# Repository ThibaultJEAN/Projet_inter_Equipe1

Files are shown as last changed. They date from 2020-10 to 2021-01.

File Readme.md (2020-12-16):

# I5AEPR11 - Projet interdisciplinaire

> Pauline Combes <br> 
> Emma Devaud <br>
> Romain Gary <br>
> Mélissa Malischewski <br>
> Xavier Bourlot <br>
> Jeremy Aubert <br>
> Clarisse Calmo <br>
> Thibault Jean  <br>
> Xiaohu Zhang <br>

#### [Drive](https://drive.google.com/drive/folders/1-SFvpA1gzc2IVzgCnODUU9VLPYTG9q0a?usp=sharing)

#### [Discord](https://discord.gg/qqvn4z)

#### [Confluence](https://espe.atlassian.net/wiki/spaces/PI/overview?homepageId=131077)

#### [Overleaf Report](https://www.overleaf.com/8144512892ybrzztqnfcqb)

### INSA Toulouse 5A 2020

---

## Buck

`schematic_initial` : Premier schéma pour identifier et calculer les composants critiques

`calculations` : Calcul des composants et contraintes, estimation des pertes

`schematic_complete` : Schéma complet avec composants de mods et indications de routage

---

## BMS

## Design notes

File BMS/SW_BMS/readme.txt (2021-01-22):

************************************************************
*							   *
*		README FILE BMS SOFTWARE		   *
*							   *
************************************************************
author: jeremy aubert for GEI Corp

Utilisation de notre API.

I- Initialisation

Nous proposons une fonction "BMSManagement_Init" permettant
l'initialisation des jauges. Cette initialisation regroupe :
	- la vérification de la bonne connexion entre le 
	microcontroleur et la jauge (avec un mode bloquant
	+ message d'erreur si pas de connexion)

	- l'écriture dans le registre de "control" du mode
	automatique. Cette écriture permet de faire une 
	mise à jour des registres (tension, courant, ...).

Une fonctionnalité n'est tout de fois pas inclu dans cette 
fonction : l'initialisation de la valeur du SOC. D'après
la documentation technique du composant LTC2944, la valeur
par défaut du SOC est de 50%. Pour le moment, il faut 
utiliser la fonction setSOC présente dans InfoBatt.c
Les paramètres à utiliser sont :
	- I2C_HandleTypeDef nb_batt : il faut utiliser
	les constantes BATTERY1 et BATTERY2.
	- uint16_t initValue : il faut entrer la valeur
	en hexadecimal selon le taux de charge de la 
	batterie. Cette valeur se fixe selon la formule
	suivante :
	     (initValue)_16=deltaQ*StateOfCharge

II- La lecture des informations se fait par la fonction 
BMSManagement_getInfo. Les paramètres sont :
	- char info : 'V' pour avoir la tension, 'I' pour
	avoir le courant, 'S' pour avoir le SOC.
	- I2C_HandleTypeDef nb_batt : il faut utiliser
	les constantes BATTERY1 et BATTERY2.

III- Fonction support

saveSOC - Afin de sauvegarder la dernière valeur de SOC
des batteries pour la sauvegarder dans une mémoire.

checkLink - A utiliser si vous souhaitez vérifier le lien
à tout moment entre le µC et la jauge.

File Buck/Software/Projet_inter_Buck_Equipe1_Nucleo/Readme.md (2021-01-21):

Indications de fonctionnement pour le code Buck :

PWM sur TIM1. Fréquence réglable par define. Duty min et max aussi. Valeurs actuelles : 150kHz, 10%, 90%
Acquisitions multiples par ADC1 avec DMA et trigger par TIM2, transfert dans les variables par interruption ADC de conversion complète. F_acq réglable par define, valeur actuelle : 5kHz

Les regulations actuelles sont des proportionnel uniquement. Régulation MPPT non fonctionnelle.

Interface Uart (debug rapide) : 
La carte affiche ses mesures toutes les 500ms.
Elle démarre en mode CV 24V.
Pour changer de mode : 'v' pour CV, 'c' pour CC, 'm' pour MPPT, 'o' pour OpenLoop
Pour changer le setpoint : '+' ou '-'. Incrément varie en fonction des modes : CV +-1V, CC +-250mA, OL +-10%.
Attention, ne pas envoyer plusieurs commandes trop rapidement, sinon le buffer panique et il faut reset la carte.

Attention, si la GUI CubeMX est utilisée pour regénérer le projet, il faut ensuite commenter les lignes 
"htim1.Init.Period = 65535;" et "//htim2.Init.Period = 999;".

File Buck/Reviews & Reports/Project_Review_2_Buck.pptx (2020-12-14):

## Smart Power Management System Review n° 2 12-11-2020 INSA Toulouse Team 1 - Buck Xavier Bourlot Thibault Jean Clarisse Calmo Xiaohu Zhang

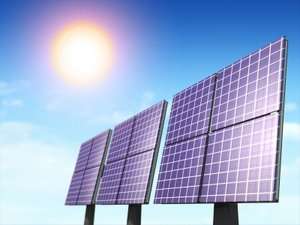
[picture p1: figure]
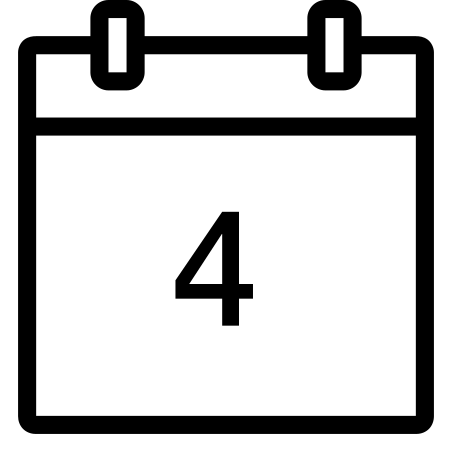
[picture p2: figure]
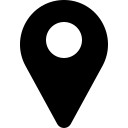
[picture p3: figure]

## TEAM PRESENTATION TEAM SKILLS :

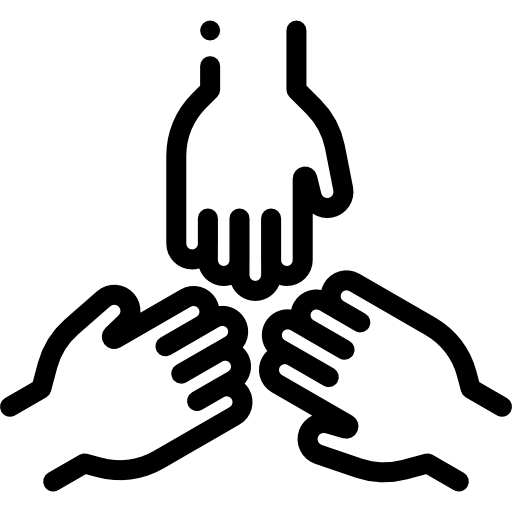
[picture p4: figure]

Team members | Roles
BOURLOT Xavier | Inspector of finished products
CALMO Clarisse | Electronics Engineer / Super Manager
JEAN Thibault | Software and Hardware Engineer
ZHANG Xiaohu | Analog Electronic Engineer

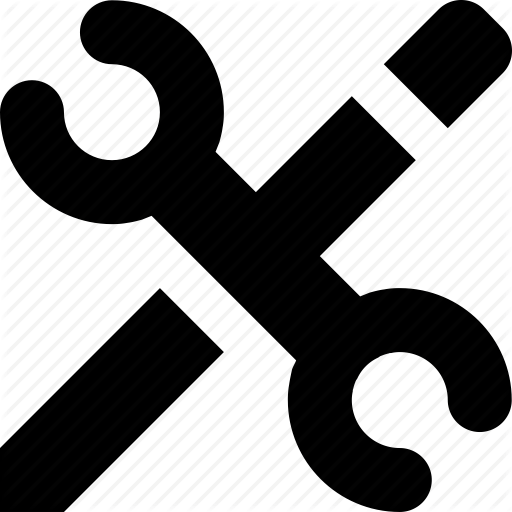
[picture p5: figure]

- Electronic system conception
- Software programming
- Prototyping
- Routing
- Project management
- Cooking

## SYSTEM OVERVIEW

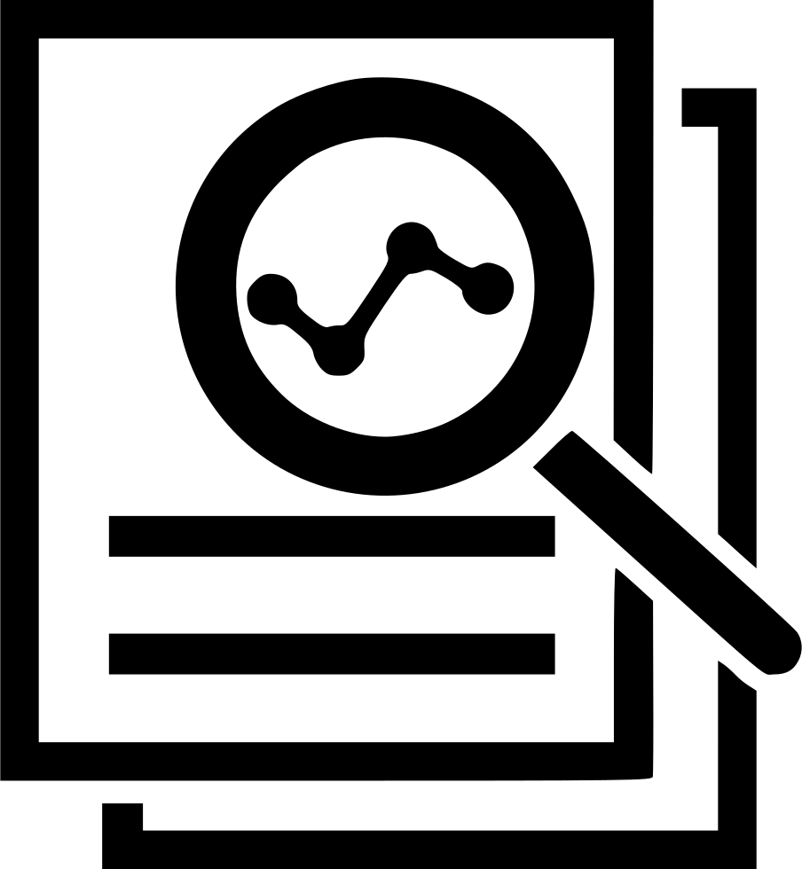
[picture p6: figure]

Smart Power Management System :
intelligent system capable of providing energy, either from power network or from solar panel.

Communicating Plugs :
charges connecting points

Solar Panel Supply Unit : autonomous power block

Buck part :
Energy converter

Our mission : implementing this sub-system.

## HARDWARE ARCHITECTURE

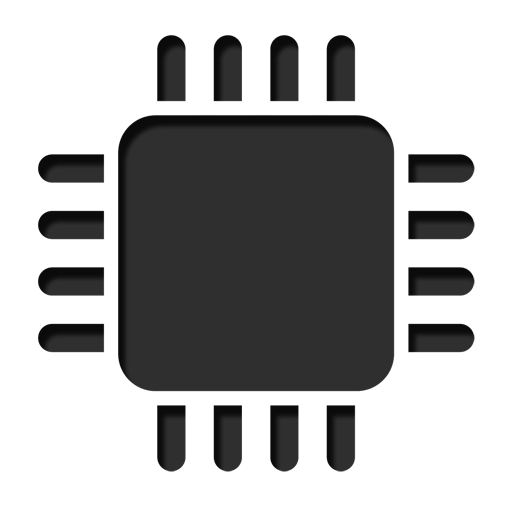
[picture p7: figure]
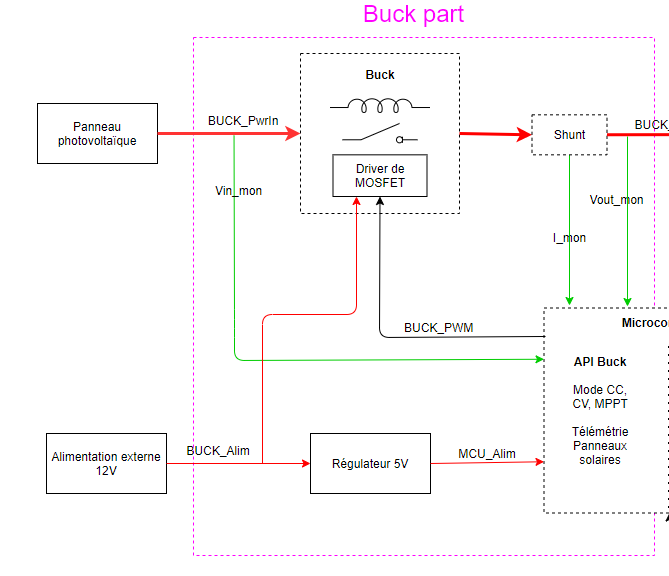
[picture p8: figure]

-Power block located right after the solar panel.
-Energy delivery : up to 200W
-Various control modes :
constant voltage,
constant current,
MPPT,
open loop (test mode)

Towards BMS

Microcontroller

## SOFTWARE ARCHITECTURE

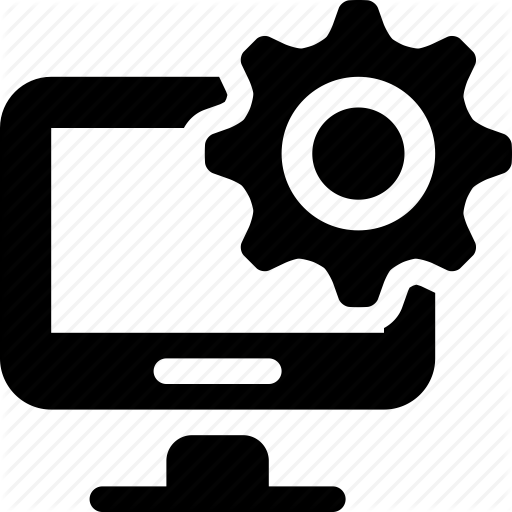
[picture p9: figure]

Software high level architecture
- Function Management_Mode : Management of the different operating modes
- Function Get_BuckOutputCurrent
- Function Get_BuckOutputVoltage
- Function Get_BuckOutputPower
- Function Get_BuckInputVoltage
These different functions are there to retrieve the quantities useful for the regulation modes.

Main specifications we are going to implement :
- The power supply will be taken first from the photovoltaic panel
- Management of the different regulation modes
- Prevention against the risks of too much power and too much discharge of the batteries

## Next steps

The future step of the project are :
- Software development on the project library as well as on the test functions
- Finish composant sizing & selection
- Continue the schematic developpement and start the PCB layout under Altium
- Making further simulations under LTSpice
- Writing a report for the final low level architecture

## Forecast schedule

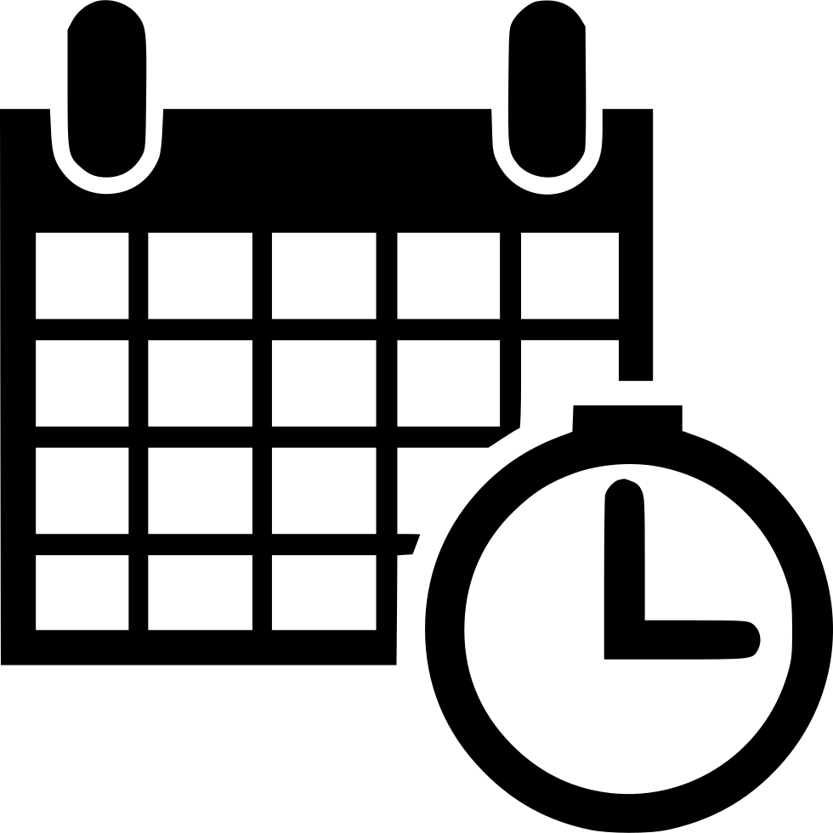
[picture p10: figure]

- This week : finalize the low level architecture
- In 2 weeks : send the final schematic & BOM
- Next month : write a report with the final software architecture
- In 2 months : boards fabrication & write a report with the unit tests

## PREVIOUS REVIEW CONTENT

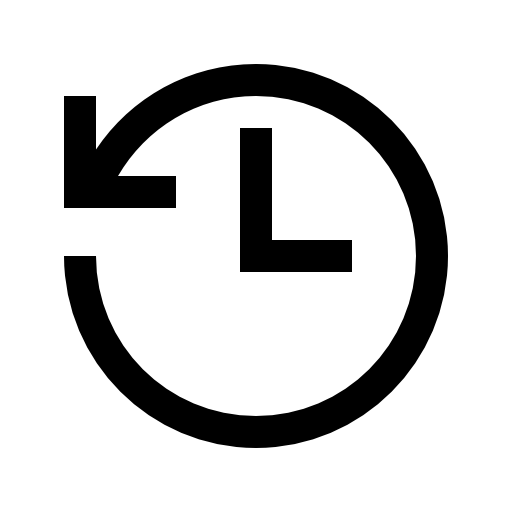
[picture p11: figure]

Last month, we introduced a summary of the work initiated :
- An overview of the smart power management system
- The team skills
- The hardware & software high level architecture
- Our planning

## HARDWARE ADVANCEMENT

Tasks performed since our last meeting :
- Finalize the low level architecture
  - Component selection & sizing
  - Schematic development
  - LTSpice simulations
- Edit project library in Altium
- Edit the BOM
- Finalize the PCB routing

## FINAL HARDWARE SCHEMATIC

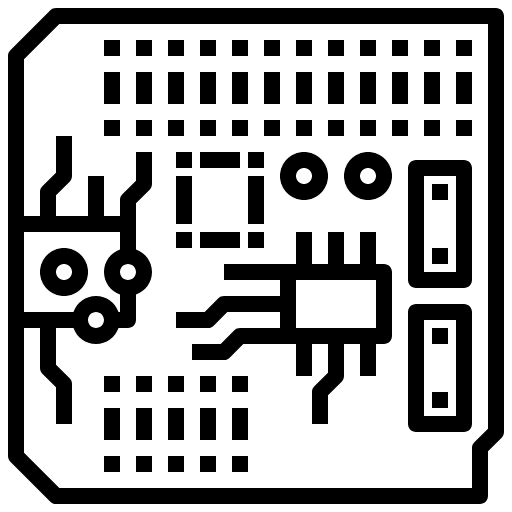
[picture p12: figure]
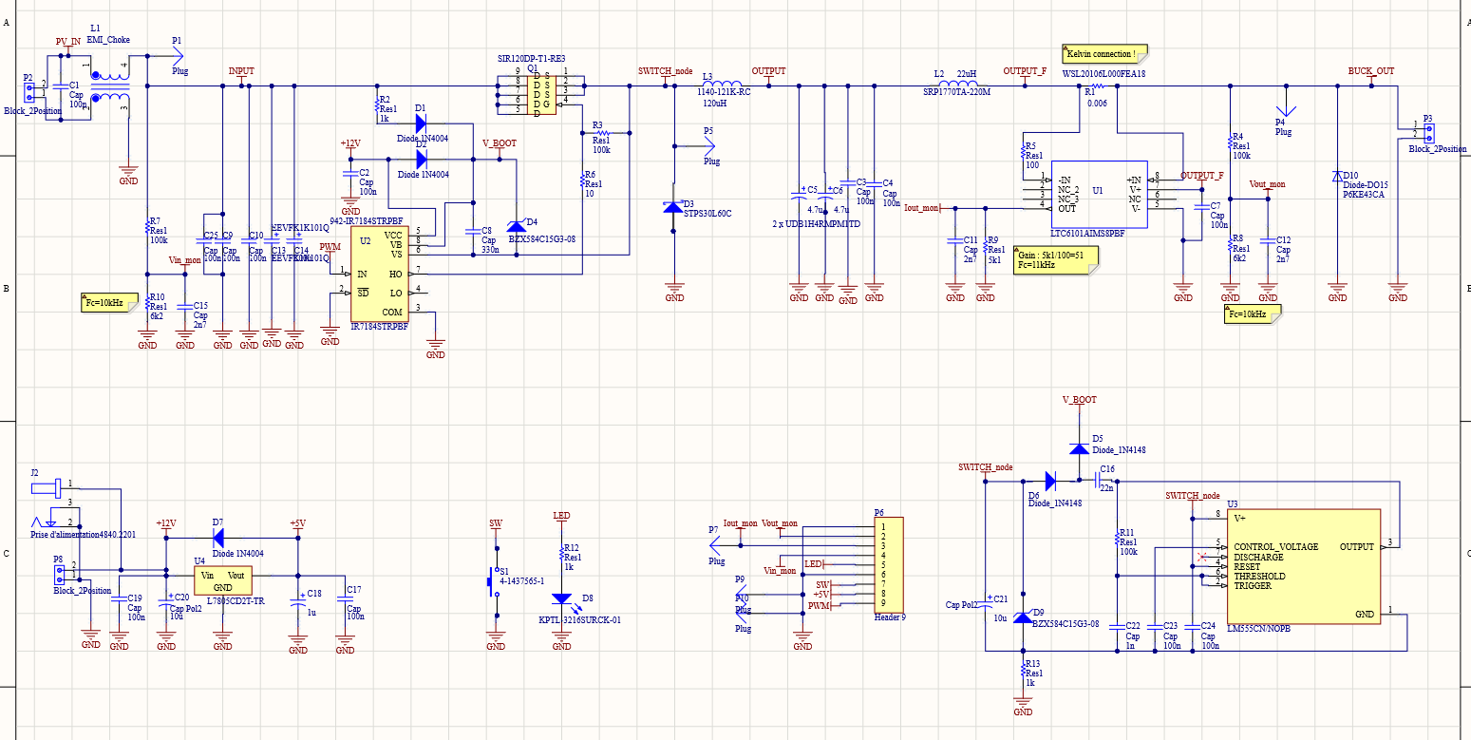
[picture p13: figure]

## ESTIMATED COSTS

- Major costs come from power components
→ power conversion
- EMI (filtering) generates important costs too
→ common mode choke
Costs reduction envisaged :
- Eliminate the external charge pump by restricting the duty cycle in software.
Unsupported costs :
The Nucleo card is shared between the BMS & Buck team.

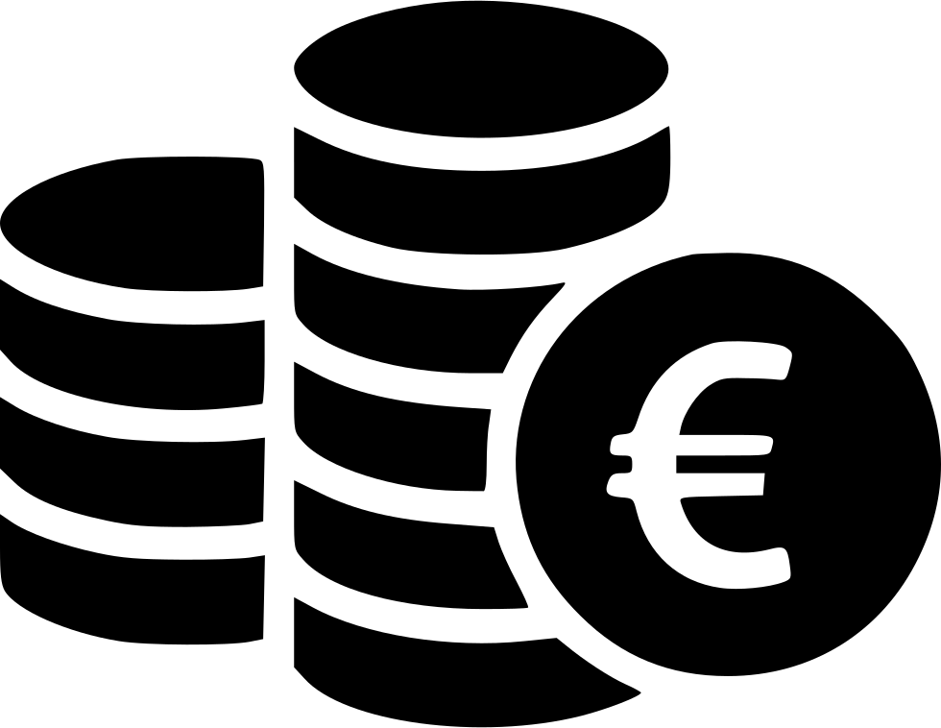
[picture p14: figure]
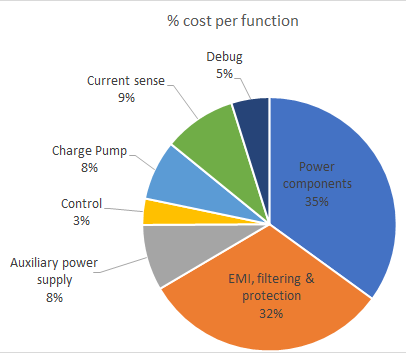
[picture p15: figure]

## PCB ROUTING -2D

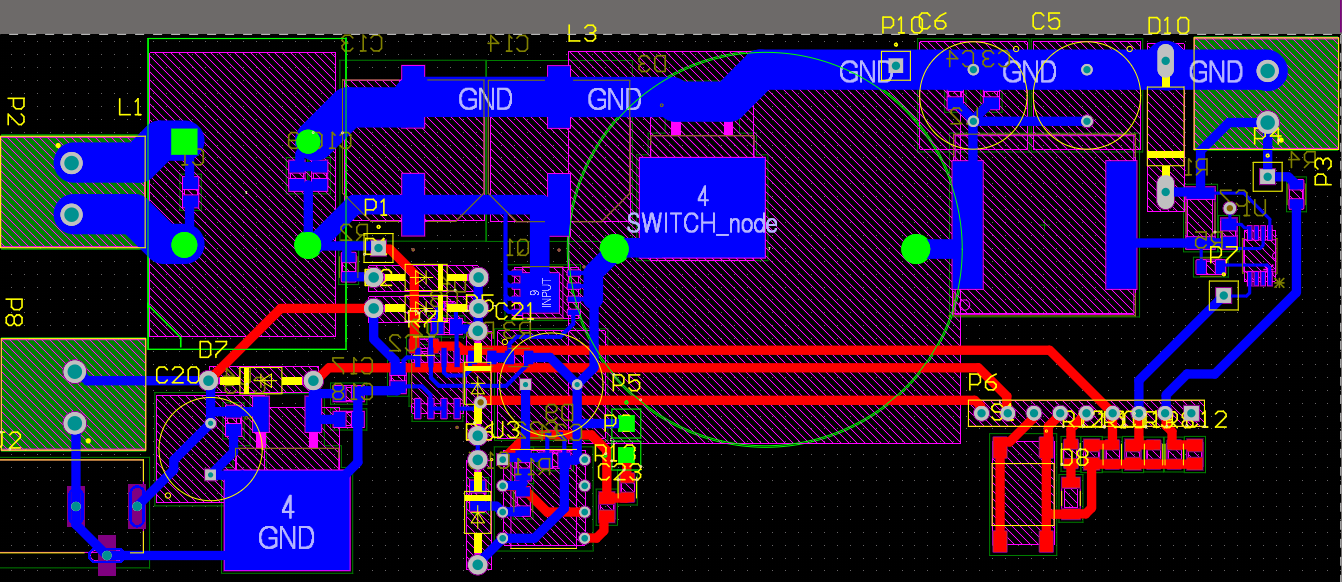
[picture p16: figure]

## PCB ROUTING -3D

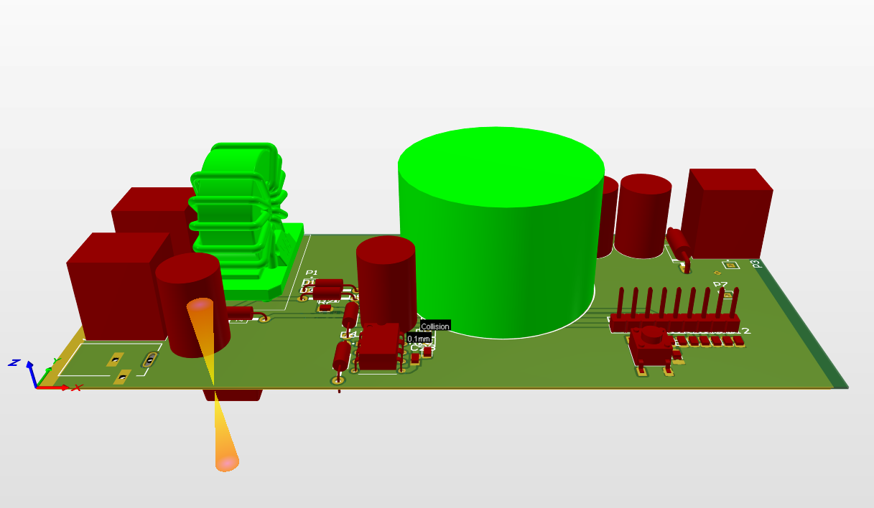
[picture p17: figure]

View of the last version of our PCB design

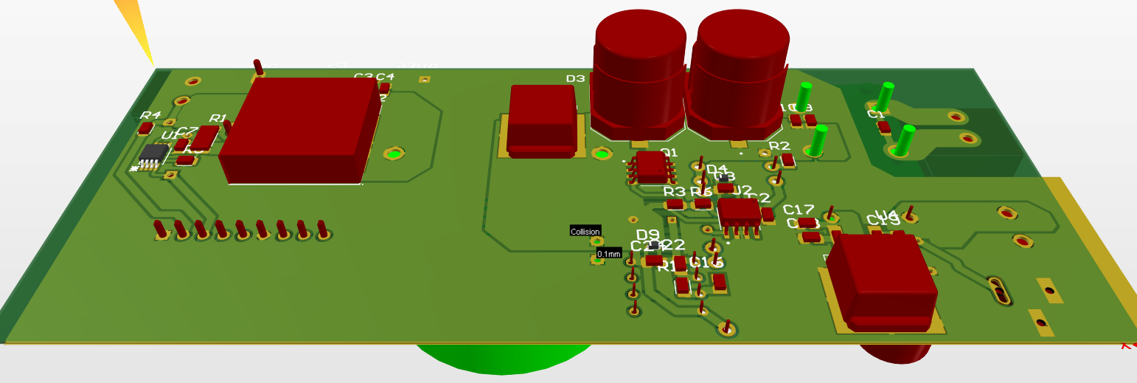
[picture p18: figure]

## SOFTWARE ADVANCEMENT

Tasks performed since our last meeting :
- Finalize the low level architecture
  - Software architecture class diagram
  - Identify functions, constants and variables.
- Start the development with STM32CubeIDE
  - Initialize our peripherals
  - Write the functions content
- Make tests with a Nucleo card
  - Test the PWM and ADC with DMA

## SOFTWARE ARCHITECTURE DIAGRAM

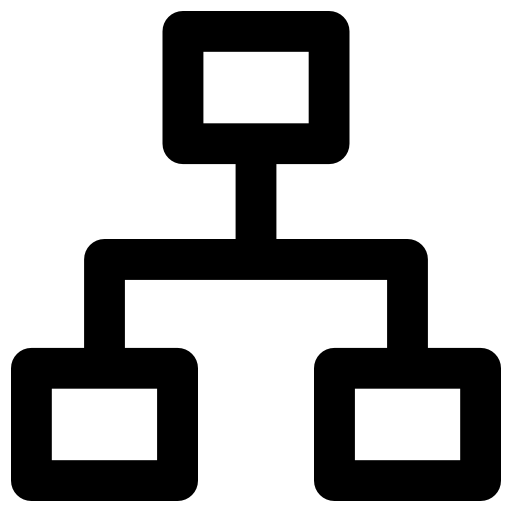
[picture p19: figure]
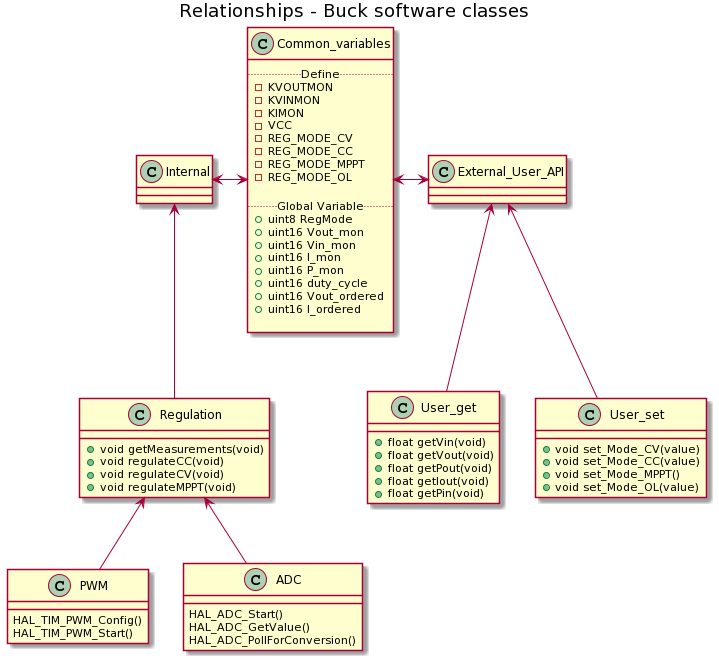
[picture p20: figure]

We are developing the software with a :
- 3-layers architecture
- High level layer dedicated to management
- Middle level layer dedicated to regulation to meet the buck specifications
- Low level layer as a link with the hardware
- 2-parts structure - Internal part for processing
-External user API

## TIME MANAGEMENT

Now, we are around 60% of the allotted time and we met the goals of our initial planning.
- Team feelings :
  - comfortable with the subject
  - confident for the final steps
- Work pace :
  - a considerable increment is done each week
  - documentation & report are regularly updated in parallel of development

## Next steps

The future steps of the project are :
- Complete the software structure
- Finish the final software architecture report
- Pursue and document software unitary tests
- Make further hardware tests in lab rooms
- Send the PCB files for production & validate design

## Thank you for your attention Do you have any question

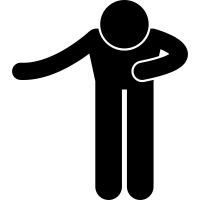
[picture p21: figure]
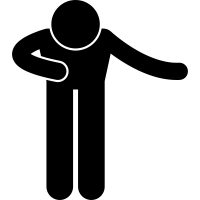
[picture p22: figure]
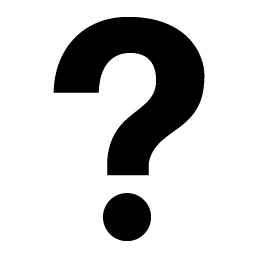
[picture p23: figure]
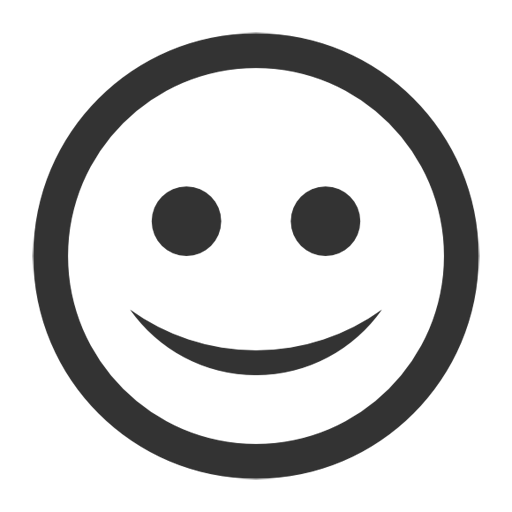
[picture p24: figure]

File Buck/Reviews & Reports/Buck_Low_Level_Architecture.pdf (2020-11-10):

Automatique Electronique ESPE

Projet Interdisciplinaire

# Buck Low Level Architecture

Authors :


Xavier Bourlot

Thibault Jean

Clarisse Calmo

Xiaohu Zhang

5AE-ESPE

Supervisors :

T. Rocacher
A. Boyer
G. Auriol
C. Escriba
J. Shea
November 6, 2020

# Contents

1 Introduction | 2
2 Hardware | 3
3 Software organisation | 8
4 Next Phase | 12
A LTSpice simulation | 13

CHAPTER 1. INTRODUCTION

# Chapter 1

# Introduction

In the Smart Power Management System, the Buck plays a central role in order to convert the energy. Our previous report explained the high level architecture of the Buck with a reminder of specifications, a list of useful signals and the main blocks on a diagram. Now, we are going to detail the buck schematic, components sizing and the software organisation.

In the hardware part, all the components are divided into two part: the power components and control functions. For the power components, we designed a preliminary switch circuit and determined the switching frequency to 150 kHz. Basing on this condition, considering other constraints, we can confirm the dimensions of components. We also design several functions which can realise the regulation to the circuit. With all the dimensions we got, we can finally build the circuit model and analog with software to inspect if the dimensions are appropriate. In the end, we build our complete schematic with Altium.
With the software part, we allow the customer to change the mode of this system according to their requirements. The customers have four options available: CV, CC, MPPT and Open loop mode. We realise the internal part and the external part by configuring the variables and functions in the software part.
Projet Interdisciplinaire | 2

# Chapter 2


In this section, we will explain our approach and design choices for components sizing, and give
our preliminary schematic, edited in Altium.

Should the LO output be terminated ?

Input PV/Output connectors ?
Power jack : 2.1 x 5.5 x 10 mm, center positive
Add test points
Serial connector ?

Figure 2.1: Low Level Hardware Architecture

CHAPTER 2. HARDWARE

- Top half, from left to right : power flow from the solar panel input to the buck output (BMS input).
- Bottom left : Auxiliary 5V power supply derived from 12V
- Bottom center : microcontroller connector & associated components
- Bottom right : charge pump for the bootstrap supply

## 2. Component selection & sizing

The following section details some of the component choices and calculations for the critical points of the design. It derives the main requirements and highlights some of the losses that the design will inherently present. No overall efficiency figure is proposed in this document, because not every loss of the design has been estimated yet, rendering any estimation difficult. However, with the main static losses taken into account, the efficiency at 150W would be less than 96% (7.25W loss).

### 2.1. Power components

The switching frequency has been selected to 150kHz, a trade-off between large components at low frequencies and higher switching losses at high frequencies. This frequency will be used for the calculations in the next paragraphs.

2.1.a. Inductor

The inductor is designed for 700mA worst case ripple current. For the worst case scenario (Vin=48V, Vout=24V), the minimum value is 120µH. Typical current ripple will be less than 500mA. The 1140-121K-RC will be selected as it satisfies the requirements for value and RMS current, and is already available in stock. It’s DCR is 28mΩ, which results in static loss of 2.27W.

2.1.b. Cout

The output capacitor must satisfy the following constraints :

- Rated voltage > 40V
- IRMS > 700mA
- C > 3µF for a maximum output voltage ripple of 0.5V
- C small enough to allow connection to the batteries & minimize overshoot at no load or during transients

Given these requirements, it is difficult to find a small value capacitor with sufficiently high

IRMS.
The UDB1H4RMPM1TD is a 4.7µF aluminium electrolytic capacitor, 50V , with tanδ = 0.15 and IRMS = 400mA. We can estimate the ESR given the tanδ : ESR = 1Ω. Two identical capacitors in parallel will double the capacitance and halve the ESR, and meet the

CHAPTER 2. HARDWARE

IRMS requirements. Using the same capacitors in parallel (and possibly matching their value) will guarantee better sharing of the ripple current between the two devices.
The expected output voltage ripple with this configuration, accounting for the ESR contri-bution, is 360mV, which meets our 500mV target.
The expected response of the L-C filter is shown in appendix, as well as the LTSpice schematic used.

2.1.c. MOSFET

The mosfet must have a low on-resistance, hold the maximum PV voltage and max current. The IRFB4115PBF fits these needs and is already in stock. At the worst case duty cycle (67%), the static power loss is approx 0.4W, due to the RdsON = 11mΩ. The estimated temperature of the case without any heatsink is then 50°C, but this does not take dynamic losses into account, which could be the main losses at stake here. These will be calculated later on to determine if heat-sinking the device is necessary.

2.1.d. Diode

The diode must have a low forward voltage to minimize power dissipation, be reasonably fast, allow for the peak current of 10A and hold a reverse voltage of 50V max. The average current through the diode is 6.75A for the worst case scenario (Duty cycle of 25% and full output current). With a typical forward voltage of 450mV at the given current, the power dissipation is approx. 3W.
Depending on the package of the chosen diode, a small heatsink may be required. By example, the STPS30L60C surface mount dual diode may satisfy the electrical requirements, but a 5cm² min area of copper would be required to maintain the junction temperature of the diode at 125 deg C, given a thermal resistance of 35 deg C/W. A TO-220 package may be better suited, as it can be mounted on a heatsink.

### 2.2. Other components

The input capacitor, protections (such as reverse polarity, EMI suppression choke, overload) are still in design and therefore not properly sized or present on the schematic for the moment. The output secondary filter inductor is still the design phase as well.

### 2.3. Control functions

Aside from the power path, several functions are required to ensure proper regulation. The calculations and choices are detailed in the following paragraph.

2.3.a. Vin & Vout sense

Two voltage dividers are used to sense the input and output voltage. Output voltage monitoring allows for constant voltage regulation, and input monitoring allows for MPPT regulation, combined with current sensing.
To ensure protection of the microcontroller analog inputs, the desired maximum measurable voltage is set to 55V, and the resistor divider current to 500µA (an order of magnitude higher

CHAPTER 2. HARDWARE

than the ADC input pin current). A capacitor is placed at the ADC input to filter the switching frequency (F−3dB = 10kHz). The following standard values are obtained :

R1 = 6.2kΩ
R2 = 100kΩ
C = 2.7nF

The same circuit will be used for both input and output voltage sensing, to minimize the number of different component values. The ADC’s 12bit resolution allows sufficient granularity in both measurements for proper regulation. Due to the small current through the divider, very little power is lost by the measurement.

V inmax = 56.5V
Resolution = 14mV
Ploss = 2 ∗ 30 = 60mW

2.3.b. Current sense

To sense the current, a shunt resistor will be used, with a corresponding current sense amplifier. The high side topology as been selected, despite of its higher common mode requirement, to ensure a single common ground across all the system, which eases probing and integration with the BMS.
The shunt resistor is selected to minimize power dissipation whilst maximizing dynamic range. WSL20106L000FEA18 is selected, as it is already available in stock and presents a good trade-off. This low ohmic value requires a careful layout, making use of Kelvin connections to ensure good accuracy.

Rshunt = 6mΩ
Pshunt = 600mW
Gmax = 55

The maximum gain is calculated to not saturate the ADC input at the maximum current of 10A. The selected current sense amplifier is the LTC6101. Here is why it fits the requirements of the application :

- Common mode requirements : measure 60mV over 24V : common mode of 52dB.

LTC6101 has a CMRR of 115dB min, 140dB typ.

So this gives an output ENOB =

115−52
6.02 = 10.4bits min, 14.6bits typ. The ADC is 12bits, which yields a current resolution of 10A
2

12 = 2.4mA, or 9.76mA for the effective 10bits −→10 bits is enough resolution.

- Input offset voltage of 150µV max, so 150µV 60mV ∗10A = 25mA equivalent to the measurement (typ. offset : 85µV , 14mA equ.)
- Gain settable with 2 resistors
- V inmax >PV max output voltage : can’t be blown up even in the worst case scenario
- Current consumption < 1mA

CHAPTER 2. HARDWARE

- $2 in single quantity, readily available from common distributors

The chosen amplifier gain will be 51, and the output current capability of the amplifier will be set to 1mA. Referring to the amplifiers datasheet, this gives :

VADCF S = 3.06V
R1 = 100Ω
R2 = 5.1kΩ

2.3.c. MOS driver

The MOS driver is imposed by the specification. A pull down resistor is added to the gate of the mosfet to ensure it is turned off by default. A series resistor is added to the gate to trim the turn on/off time of the MOS and limit the driver output current.
The N-MOS has to be driven with a floating voltage because its source is on the switching node. Therefore, a bootstrap supply has to be generated from the auxiliary 12V supply. The bootstrap capacitor is selected given the gate minimum voltage of 7V and charge (120nC) of the mosfet.

C >

2(2 ∗ Qg +

Iqbs

Fsw

)
Vcc − V f − V min

=

2 ∗ (2 ∗ 120nC +

150µA)
100kHz
12 − 0.7 − 7

= 112nF

A 330nF capacitor will be selected. The bootstrap diode must be able to withstand approx 50V and 120nC ∗ 100kHz = 120mA, with little reverse leakage. The 1N4148 with its 200mA limit and fast response time is enough for this application.

2.3.d. Bootstrap supply

An external bootstrap supply will be provided to ensure proper MOS drive even at 100% duty cycle. The implementation will reuse an existing design based around a floating 555 IC.

2.3.e. Power supply

From the auxiliary 12V supply, a 5V supply is derived to power the microcontroller. A linear regulator is used, with its associated decoupling capacitors. No reverse input polarity protection is implemented because the power jack can’t physically be reversed.

CHAPTER 3. SOFTWARE ORGANISATION

# Chapter 3

# Software organisation

In this section, we will give a detailed architecture of the software part.

## 1. Architecture overview

First, here is a class diagram of the software organisation Figure 3.1. In this diagram we can see two main parts referring to the internal processes and the external API. We will comment and explain this diagram in the next sections.


Figure 3.1: Low Level Software Architecture

CHAPTER 3. SOFTWARE ORGANISATION

## 2. Software layers

If we analyse the diagram by rows, we can notice that each rows refers to a software layer.

### 2.1. High level layer

The first row at the top refers to the high level layer, with on one hand the user interface, and on the other hand the internal management. These two parts do not communicate with a direct relationship, but through shared variables.

### 2.2. Middle level layer

The second row in the middle refers to the different functions used to meet the Buck specifications. On the left side, we can see the internals fonctions used for the regulation (CC, CV or MPPT). On the right side, we have the functions available in the user API, for getting signal values or for setting a specific mode.

### 2.3. Low level layer

The third and last row refers to the hardware layer. Theses classes are located on the left because this layer only makes sense in the internal side that communicates with the physical board. This last layer is about communication with the buck, so we will use HAL functions for the PWM or the ADC.

## 3. Contants and variables

In the first row of the Figure 3.1, the central block contains our constants and variables.

### 3.1. Constants

We set several "Define" for constants values used all along the code. The three first values refers to signals values coefficient conversion. KVOUTMON and KVINMON refer to the divider bridges at the input and the output of the buck, in order to fit the microcontroller voltage range. Next, we have KIMON that helps reading the output current thanks to the shunt resistance, and VCC which is 3.3V. Finally, the last four constants are the regulation mode values, REG_MODE_CV, REG_MODE_CC, REG_MODE_MPPT, REG_MODE_OL (OL for Open Loop), which are respectively 0,1,2,3.

### 3.2. Variables

In addition, we have several variables that can be modified by the internal and the external part as mentioned before. With these variables, we are able to store and update the values of the current regulation mode with RegMode, or the different signals values Vout_mon, Vin_mon, I_mon. We also compute and store the output power P_mon and the duty cyle duty_cyle. Finally, we have the targeted voltage Vout_ordered and current I_ordered values used for CV and CC regulation.

CHAPTER 3. SOFTWARE ORGANISATION

## 4. Classes and functions

### 4.1. Regulation Class

In this class, we use four functions aimed to regulate the buck. First, the regulation implies hav-ing the different signals values so the function getMeasurements() recovers thoses values. Sec-ondly, we have three regulation functions, regulateCC(), regulateCV(), regulateMPPT() that adjust the duty cycle value. Regarding the code architecture, we will implement a switch case block that reads the value of the mode variable RegMode, and then calls the associated regulation function. These functions are type void and they do not take any parameter.

### 4.2. User Classes

User classes are separated in two parts : one for accessing signal values, and the other for setting a regulation mode.

### 4.3. Getter

We have five functions available in the API, so that the user can recover the value of :
- the output current getIout()
- the input and output voltage getVin() and getVout()
- the input and output power getPin() and getPout()
These functions return a float and they do not take any parameter. They work by reading the the actual signal value stored in the global variables. Therefore, they do not directly read the ADC but return the last sampled value.

### 4.4. Setter

We have four function available in the API, so that the user can choose which regulation mode to apply :
- CV regulation set_Mode_CV(value)
- CC regulation set_Mode_CC(value)
- MPPT regulation set_Mode_MPPT()
- Open loop mode set_Mode_OL(value)
These functions are of type void because they do not return anything, these functions are there to allow the client/users to change the regulation mode of the system so we have chosen not to return anything because the client will see the change live on the physical system. Each of these functions take as argument a variable that we have called "value", it is the target value of the quantity useful for the regulation of the buck. For example, CV regulation will take a voltage value, CC regulation will take a current value. In the case of MPPT regulation, we take no argument because this regulation aims to send as much power as we can from the photovoltaic panel therefore no need to have a target value because it is the maximum power extracted from the panel that will be taken.

CHAPTER 3. SOFTWARE ORGANISATION

## 5. Use case example

Here, we are going to illustrate the use of these functions and variable through an concrete example.
We will take as an example, the system in CV regulation mode, the costumer wants to change the regulation mode and switch to MPPT regulation, he will therefore interact with the system to be able to change the current regulation. The client will dialogue with external part of the system, he will ask the Set_Mode_MPPT system without giving any argument, we are currently in the right side of Figure 3.1. Following this function, the External_User_API will change the value of the global variable RegMode and will set it to the value which corresponds to the MPPT regulation thanks to the internal part will be able to read the new value of the global variable RegMode and change the regulation of the buck through the regulateMPPT function. We are now in the left side of Figure 3.1. Through this mechanism of external and internal part, we limit the interactions between the user and the microcontroller. In order to be able to have information on the changes taking place, the customer can use the different Get functions available to him.

CHAPTER 4. NEXT PHASE

# Chapter 4

# Next Phase

As we have a complete low level architecture, we will now focus on the actual realisation of the project. The software development will be about the project library and also test functions. In parallel, we will pursue the PCB layout on Altium and make further simulations on LT Spice. In two weeks we will deliver the schematic and the BOM (Bill of Materials), which will show the complete circuit and all the components needed. Next month we will write a report with the final software architecture. We predict that we will put our boards into fabrication in two months. Our team will work effectively to properly reach those goals and satisfy the client wishes.

APPENDIX A. LTSPICE SIMULATION

# Appendix A

# LTSpice simulation


Figure A.1: LTSPICE schematic for simulation


(a) At startup | (b) Steady state

Figure A.2: Output Current & Voltages

V (n002) is the voltage across Cout. Note the small current overshoot, and the improved voltage ripple at V (out).

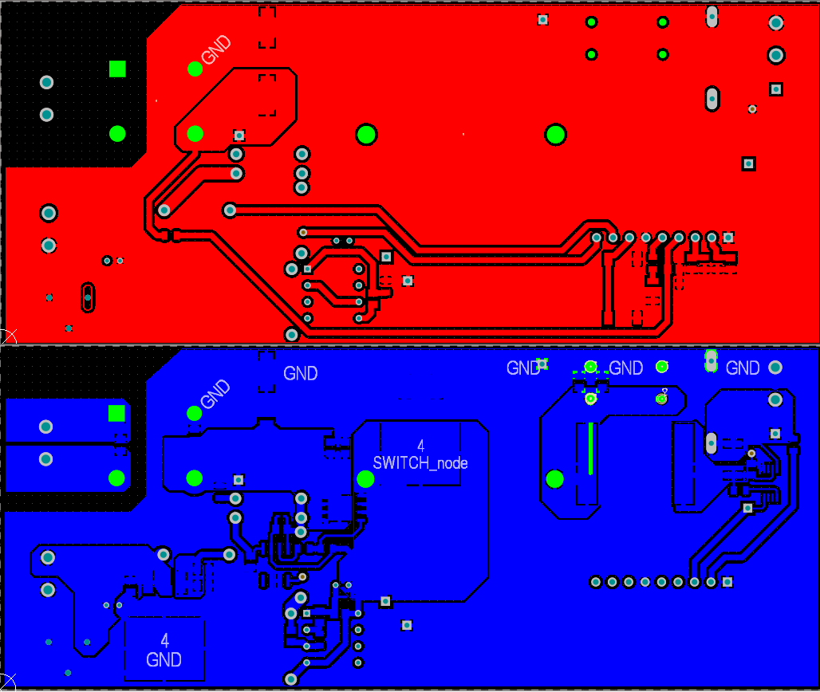
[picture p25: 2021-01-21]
Buck/schematic_complete/Buck/layout_top_bottom.png

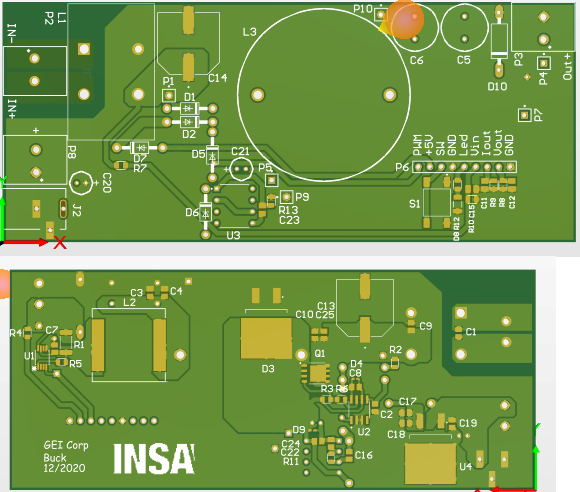
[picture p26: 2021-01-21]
Buck/schematic_complete/Buck/bare_pcb.png

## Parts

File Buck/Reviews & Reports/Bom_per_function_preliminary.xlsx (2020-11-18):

Ref | Designator | Package | Description | Qty | Value | Unit price | Price($,1000qty) | Percentage
Power components |  |  |  |  |  |  | 16.90 | 39.54015999% | Power components | 39.54015999%
EEVFK1K101Q | C7 | POLAR0.8 | Cap Pol2 | 1 | 100u | 1.38 | 1.38 | 3.227768162% | EMI filtering & protection | 30.78074566%
1140-121K-RC | L1 | 0402-A | Inductor | 1 | 120uH | 6.03 | 6.03 | 14.10394349% | Debug functions | 0.8396875146%
SRP1770TA-220M | L2 | 0402-A | Inductor | 1 | 10uH | 2.74 | 2.74 | 6.408757075% | Auxilliary Power supply | 7.835524161%
STPS30L60C | D2 | SMB | D Schottky | 1 |  | 1.11 | 1.11 | 2.596248304% | Charge Pump | 7.50806942%
PV_IN, BUCK_OUT | P1, P2, P4 | CON1X2 | 2 Pin PWR CON | 2 |  | 0.75 | 1.50 | 3.508443654% | Current sense | 8.604437569%
SIR120DP-T1-RE3 | Q1 | E3 | MOSFET-N | 1 |  | 0.655 | 0.66 | 1.532020396% | Control | 5.169106984%
IR7184STRPBF | U2 | SOIC127P600X175-8N | IR7184STRPBF | 1 |  | 1.73 | 1.73 | 4.046405015%
1N4148, 1N4004 | D1, D5, D6, D7 | DO-41 | Diode 1N4004 | 1 |  | 0.19 | 0.19 | 0.4444028629%
Res1 | R6 | AXIAL-0.3 | Res1 | 1 | 10 | 0.17 | 0.17 | 0.3976236142%
UDB1H4RMPM1TD | C1, C2 | POLAR0.8 | Cap Pol2 | 2 | 4.7u | 0.7 | 1.40 | 3.274547411%
EMI filtering & protection |  |  |  |  |  |  | 13.16 | 30.78074566%
Inductor | L3 | WE-CMBNC_Type | 7448042001 | 1 | 1mH | 11.39 | 11.39 | 26.64078215%
P6KE43CA | D3 | SMC | TVS Diode | 1 |  | 0.39 | 0.39 | 0.9121953501%
EEVFK1K101Q | C7 | POLAR0.8 | Cap Pol2 | 1 | 100u | 1.38 | 1.38 | 3.227768162%
Debug functions |  |  |  |  |  |  | 0.36 | 0.8396875146%
4-1437565-1 | S1 | SPST-2 | SW-PB | 1 |  | 0.006 | 0.01 | 0.01403377462%
KPTL-3216SURCK-01 | D9 | 3.2X1.6X1.1 | LED2 | 1 |  | 0.183 | 0.18 | 0.4280301258%
Res1 | R4, R12, R13 | AXIAL-0.3 | Res1 | 1 | 1k | 0.17 | 0.17 | 0.3976236142%
Auxilliary Power supply |  |  |  |  |  |  | 3.35 | 7.835524161%
L7805CD2T-TR | U4 | D2PAK_N | Volt Reg | 1 |  | 0.8 | 0.80 | 1.871169949%
12V_IN | P1, P2, P4 | HDR1X2 | Header 2 | 1 |  | 0.75 | 0.75 | 1.754221827%
Cap Pol2 | C16 | POLAR0.8 | Cap Pol2 | 1 | 10u | 0.72 | 0.72 | 1.684052954%
Cap | C8 | RAD-0.3 | Cap | 1 | 1u | 0.38 | 0.38 | 0.8888057258%
1N4148, 1N4004 | D1, D5, D6, D7 | DO-41 | Diode 1N4004 | 1 |  | 0.19 | 0.19 | 0.4444028629%
Res1 | R4, R12, R13 | AXIAL-0.3 | Res1 | 3 | 1k | 0.17 | 0.51 | 1.192870842%
Charge Pump |  |  |  |  |  |  | 3.21 | 7.50806942%
1N4148, 1N4004 | D1, D5, D6, D7 | DO-41 | Diode 1N4004 | 2 |  | 0.19 | 0.38 | 0.8888057258%
LM555CN/NOPB | U3 | DIP794W45P254 | LM555CN/NOPB | 1 |  | 1.14 | 1.14 | 2.666417177%
Res1 | R2, R3, R7, R11 | AXIAL-0.3 | Res1 | 2 | 100k | 0.17 | 0.34 | 0.7952472283%
BZX584C15G3-08 | D4, D8 | DIODE-0.7 | D Zener | 1 |  | 0.29 | 0.29 | 0.6782991065%
Res1 | R4, R12, R13 | AXIAL-0.3 | Res1 | 2 | 1k | 0.17 | 0.34 | 0.7952472283%
Cap Pol2 | C16 | POLAR0.8 | Cap Pol2 | 1 | 10u | 0.72 | 0.72 | 1.684052954%
Current sense |  |  |  |  |  |  | 3.56 | 8.326706273%
WSL20106L000FEA18 | R1 | AXIAL-0.3 | Res1 | 1 | 0.006 | 1.72 | 1.72 | 4.02301539%
Res1 | R9 | AXIAL-0.3 | Res1 | 1 | 5k1 | 0.17 | 0.17 | 0.3976236142%
Res1 | R5 | AXIAL-0.3 | Res1 | 1 | 100 | 0.17 | 0.17 | 0.3976236142%
LTC6101AIMS8PBF | U1 | MSOP-8_MS | LTC6101AIMS8PBF | 1 |  | 1.5 | 1.50 | 3.508443654%
Control |  |  |  |  |  |  | 2.21 | 5.169106984%
MHDR1X9 | P3 | MHDR1X9 | MHDR1X9 | 1 |  | 0.39 | 0.39 | 0.9121953501%
Res1 | R2, R3, R7, R11 | AXIAL-0.3 | Res1 | 2 | 100k | 0.17 | 0.34 | 0.7952472283%
Res1 | R8, R10 | AXIAL-0.3 | Res1 | 2 | 6k2 | 0.17 | 0.34 | 0.7952472283%
Cap | C10, C11, C13 | RAD-0.3 | Cap | 3 | 2n7 | 0.38 | 1.14 | 2.666417177%
 |  |  |  |  |  | Total | 42.75 | 100%

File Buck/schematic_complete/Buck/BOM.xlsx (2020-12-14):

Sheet: BOM
en stock BE | Ref | Description | Designator | Package | LibRef | Quantity | Value | UnitPrice $ | Total price $ | Reference de farnell | Reference de Mouser | Reference de RS Component
x | Cap | Capacitor | C1, C4, C5, C6, C9, C10, C14, C15, C18, C21, C22 | C0805 | Cap | 11 | 100n | 0.28 | 3.08
achat | UDB1H4R7MPM1TD | Electrolytic Capacitor | C2, C3 | Thru | Cap Pol2 | 2 | 4.7u | 1.4 | 2.8 |  | 647-UDB1H4R7MPM1TD
x | Cap | Capacitor | C7 | C0805 | Cap_2 | 1 | 220n | 0.28 | 0.28
x | EEVFK1K101Q | Polarized Capacitor | C8 | SMD | Cap Pol2_1 | 1 | 100u | 1.38 | =I5*G5
x | Cap | Capacitor | C11, C12, C13 | C0805 | Cap_1 | 3 | 2n7 | 0.28 | 0.84
x | Cap Pol2 | Polarized Capacitor | C16, C19 | Thru | Cap Pol2_2 | 2 | 10u | 0.72 | 1.44
x | Cap | Capacitor | C17 | C0805 | C_4 | 1 | 1u | 0.28 | 0.28
x | Cap | Capacitor | C20 | C0805 | Cap_3 | 1 | 1n | 0.28 | 0.28
x | Diode 1N4148 | General Purpose Signal Diode | D1, D5, D6 | Diode 1N4148 | Diode 1N4148 | 3 |  | 0.19 | 0.57
x | P6KE43CA | TVS Diode, 43V | D2 | DO-15 | P6KE43CA | 1 |  | 0.39 | 0.39
x | Diode 1N4004 | 1 Amp General Purpose Rectifier | D7 | DO-41 | Diode 1N4004 | 1 |  | 0.19 | 0.19
x | STPS30L60C | 60V 30A Schottky | D3 | TO262 | D Schottky | 1 |  | 1.11 | 1.11
x | BZX584C15G3-08 | Zener Diode 15V | D4, D9 | diode_zener | D Zener | 2 |  | 0.29 | 0.58
x | KPTL-3216SURCK-01 | KINGBRIGHT RED LED | D8 | SMD | LED2 | 1 |  | 1.83 | 1.83
achat | Schurter 4840.2201 | DC Plug/Socket | J2 | Thru | 4840.2201 | 1 |  | 1.62 | 1.62 | 3282173 | 693-4840.2201 | 869-3221
x | 7448042001 | WURTH 1mH 20A | L1 | EMI_Choke | EMI_Choke | 1 | 1mH | 11.39 | 11.39
x | SRP1770TA-220M | 12A sat | L2 | SMD | SRP1770TA-220M | 1 | 22uH | 2.74 | 2.74
x | 1140-121K-RC | 29mm pitch 10A sat | L3 | L_inductor | Inductor | 1 | 120uH | 6.03 | 6.03
x | Plug | Test point | P1, P4, P5, P7, P9, P10 | HDR1X1 | Test point | 6 |  | 0.05 | 0.3
x | Block_2Position | 2WAY Screw term | P2, P3, P8 | Block_2Position | Block_2Position | 3 |  | 0.75 | 2.25
x | Header 9 | Header, 9-Pin, ,1'' pitch | P6 | HDR1X9 | Header 9 | 1 |  | 0.39 | 0.39
x | SIR120DP-T1-RE3 | 106A 80V 3.6mOhm | Q1 | SOIC-8 | SIR120DP-T1-RE3 | 1 |  | 0.66 | 0.66
x | WSL20106L000FEA18 | Resistor | R1 | 2010 | Res1_2 | 1 | 0.006 | 1.72 | 1.72
 | Res1 | Resistor | R2, R12, R13 | R0805 | Res1_6 | 3 | 1k | 0.17 | 0.51
x | Res1 | Resistor | R3, R4, R7, R11 | R0805 | Res1 | 4 | 100k | 0.17 | 0.68
x | Res1 | Resistor | R6 | R0805 | Res1_5 | 1 | 10 | 0.17 | 0.17
x | Res1 | Resistor | R8, R10 | R0805 | Res1_1 | 2 | 6k2 | 0.17 | 0.34
x | Res1 | Resistor | R9 | R0805 | Res1_4 | 1 | 5k1 | 0.17 | 0.17
x | 4-1437565-1 | Switch | S1 | SMD | SW-PB | 1 |  | 0.06 | 0.06
achat | LTC6101AIMS8PBF | Current Sense Amp | U1 | 8-MSOP | LTC6101AIMS8PBF | 1 |  | 1.9 | 1.9 | 2294755 | 584-LTC6101AIMS8#PBF | 884-6807
x | IR7184STRPBF | MOS Driver | U2 | SOIC-8 | IR7184STRPBF | 1 |  | 1.73 | 1.73
x | LM555CN/NOPB | General Purpose Timer | U3 | DIP-8 | LM555CN/NOPB | 1 |  | 1.14 | 1.14
x | L7805CD2T-TR | 5V Voltage Regulator | U4 | D2PAK | Volt Reg | 1 |  | 0.8 | 0.8
achat | PJ-006A | 2.1mm DC Power Jack | J1 | Thru | PJ-006A | 1 |  | 0.78 | 0.78 |  | 490-PJ-006A
x |  |  | R5 | R0805 |  | 1 | 100
 |  | *Prices are for single qty and subject to changes
 |  | IL Y A UNE SECONDE FEUILLE !

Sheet: ACHATS
Ref | Description | Designator | Package | LibRef | Quantity | Value | Reference Farnell | Reference Mouser | Reference RS Component
UDB1H4R7MPM1TD | Electrolytic Capacitor | C2, C3 | Thru | Cap Pol2 | 2 | 4.7u |  | 647-UDB1H4R7MPM1TD
Cap | Ceramic capacitor 35V | C7 | C0805 | Cap_2 | 1 | 220n | 3273589 | 963-GMK212BJ224KGHT | 184-3868
Cap | Ceramic capacitor | C11, C12, C13 | C0805 | Cap_1 | 3 | 2n7 | 2905462RL | 80-C0805S272K5RAUTO
Schurter 4840.2201 | 2,1mm DC Jack | J2 | Thru | 4840.2201 | 1 |  | 3282173 | 693-4840.2201 | 869-3221
Res1 | Resistor | R6 | R0805 | Res1_5 | 1 | 10 | 3464663 | 652-CHP0805AFX10R0EL
LTC6101AIMS8PBF | Current Sense Amp | U1 | 8-MSOP | LTC6101AIMS8PBF | 1 |  | 2294755 | 584-LTC6101AIMS8#PBF | 884-6807

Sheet: Function
Ref | Description | Designator | Package | LibRef | Quantity | Value | UnitPrice $ | Total price $ | % Total price
Power components |  |  |  |  |  |  |  |  |  | Power components | 34.98973306%
UDB1H4R7MPM1TD | Electrolytic Capacitor | C2, C3 | Thru | Cap Pol2 | 2 | 4.7u | 1.4 | 2.8 | 5.749486653% | EMI, filtering & protection | 31.54004107%
STPS30L60C | 60V 30A Schottky | D3 | TO262 | D Schottky | 1 |  | 1.11 | 1.11 | 2.27926078% | Auxiliary power supply | 8.377823409%
1140-121K-RC | 29mm pitch 10A sat | L3 | L_inductor | Inductor | 1 | 120uH | 6.03 | 6.03 | 12.38193018% | Control | 3.347022587%
SIR120DP-T1-RE3 | 106A 80V 3.6mOhm | Q1 | SOIC-8 | SIR120DP-T1-RE3 | 1 |  | 0.66 | 0.66 | 1.35523614% | Charge Pump | 7.618069815%
Block_2Position | 2WAY Screw term | P2, P3, P8 | Block_2Position | Block_2Position | 2 |  | 0.75 | 1.5 | 3.080082136% | Current sense | 9.281314168%
IR7184STRPBF | MOS Driver | U2 | SOIC-8 | IR7184STRPBF | 1 |  | 1.73 | 1.73 | 3.552361396% | Debug | 4.845995893%
Res1 | Resistor | R6 | R0805 | Res1_5 | 1 | 10 | 0.17 | 0.17 | 0.3490759754%
BZX584C15G3-08 | Zener Diode 15V | D4, D9 | diode_zener | D Zener | 1 |  | 0.29 | 0.29 | 0.5954825462%
Res1 | Resistor | R2, R12, R13 | R0805 | Res1_6 | 1 | 1k | 0.17 | 0.17 | 0.3490759754%
Res1 | Resistor | R3, R4, R5, R7, R11 | R0805 | Res1 | 1 | 100k | 0.17 | 0.17 | 0.3490759754%
Diode 1N4148 | General Purpose Signal Diode | D1, D5, D6 | Diode 1N4148 | Diode 1N4148 | 1 |  | 0.19 | 0.19 | 0.3901437372%
Cap | Capacitor | C1, C4, C5, C6, C9, C10, C14, C15, C18, C21, C22 | C0805 | Cap | 2 | 100n | 0.28 | 0.56 | 1.149897331%
Cap | Capacitor | C7 | C0805 | Cap_2 | 1 | 220n | 0.28 | 0.28 | 0.5749486653%
EEVFK1K101Q | Polarized Capacitor | C8 | SMD | Cap Pol2_1 | 1 | 100u | 1.38 | 1.38 | 2.833675565%
 |  |  |  |  |  |  |  | 17.04 | 34.98973306%
EMI, filtering & protection
P6KE43CA | TVS Diode, 43V | D2 | DO-15 | P6KE43CA | 1 |  | 0.39 | 0.39 | 0.8008213552% | - Power components : part majoritaire : normal car produit de conversion d'énergie
7448042001 | WURTH 1mH 20A | L1 | EMI_Choke | EMI_Choke | 1 | 1mH | 11.39 | 11.39 | 23.38809035% | - EMI à 32% ! Principalement lié au coût du common mode choke (23%): a revoir
SRP1770TA-220M | 12A sat | L2 | SMD | SRP1770TA-220M | 1 | 22uH | 2.74 | 2.74 | 5.626283368% | - Charge Pump : 8% du budget qui peuvent être éliminés par une limitation software du duty cycle
Cap | Capacitor | C1, C4, C5, C6, C9, C10, C14, C15, C18, C21, C22 | C0805 | Cap | 3 | 100n | 0.28 | 0.84 | 1.724845996% | Attention : dans control, la nucléo n'est pas prise en compte (partagée entre les != blocs
 |  |  |  |  |  |  |  | 15.36 | 31.54004107%
Auxiliary power supply
Block_2Position | 2WAY Screw term | P2, P3, P8 | Block_2Position | Block_2Position | 1 |  | 0.75 | 0.75 | 1.540041068%
L7805CD2T-TR | 5V Voltage Regulator | U4 | D2PAK | Volt Reg | 1 |  | 0.8 | 0.8 | 1.642710472%
PJ-006A | 2.1mm DC Power Jack | J1 | Thru | PJ-006A | 1 |  | 0.78 | 0.78 | 1.60164271%
Diode 1N4004 | 1 Amp General Purpose Rectifier | D7 | DO-41 | Diode 1N4004 | 1 |  | 0.19 | 0.19 | 0.3901437372%
Cap | Capacitor | C1, C4, C5, C6, C9, C10, C14, C15, C18, C21, C22 | C0805 | Cap | 2 | 100n | 0.28 | 0.56 | 1.149897331%
Cap | Capacitor | C17 | C0805 | C_4 | 1 | 1u | 0.28 | 0.28 | 0.5749486653%
Cap Pol2 | Polarized Capacitor | C16, C19 | Thru | Cap Pol2_2 | 1 | 10u | 0.72 | 0.72 | 1.478439425%
 |  |  |  |  |  |  |  | 4.08 | 8.377823409%
Control
Res1 | Resistor | R3, R4, R5, R7, R11 | R0805 | Res1 | 2 | 100k | 0.17 | 0.34 | 0.6981519507%
Cap | Capacitor | C11, C12, C13 | C0805 | Cap_1 | 2 | 2n7 | 0.28 | 0.56 | 1.149897331%
Res1 | Resistor | R8, R10 | R0805 | Res1_1 | 2 | 6k2 | 0.17 | 0.34 | 0.6981519507%
Header 9 | Header, 9-Pin, ,1'' pitch | P6 | HDR1X9 | Header 9 | 1 |  | 0.39 | 0.39 | 0.8008213552%
 |  |  |  |  |  |  |  | 1.63 | 3.347022587%
Charge Pump
Diode 1N4148 | General Purpose Signal Diode | D1, D5, D6 | Diode 1N4148 | Diode 1N4148 | 2 |  | 0.19 | 0.38 | 0.7802874743%
BZX584C15G3-08 | Zener Diode 15V | D4, D9 | diode_zener | D Zener | 1 |  | 0.29 | 0.29 | 0.5954825462%
LM555CN/NOPB | General Purpose Timer | U3 | DIP-8 | LM555CN/NOPB | 1 |  | 1.14 | 1.14 | 2.340862423%
Res1 | Resistor | R2, R12, R13 | R0805 | Res1_6 | 1 | 1k | 0.17 | 0.17 | 0.3490759754%
Cap Pol2 | Polarized Capacitor | C16, C19 | Thru | Cap Pol2_2 | 1 | 10u | 0.72 | 0.72 | 1.478439425%
Res1 | Resistor | R3, R4, R5, R7, R11 | R0805 | Res1 | 1 | 100k | 0.17 | 0.17 | 0.3490759754%
Cap | Capacitor | C20 | C0805 | Cap_3 | 1 | 1n | 0.28 | 0.28 | 0.5749486653%
Cap | Capacitor | C1, C4, C5, C6, C9, C10, C14, C15, C18, C21, C22 | C0805 | Cap | 2 | 100n | 0.28 | 0.56 | 1.149897331%
 |  |  |  |  |  |  |  | 3.71 | 7.618069815%
Current sense
LTC6101AIMS8PBF | Current Sense Amp | U1 | 8-MSOP | LTC6101AIMS8PBF | 1 |  | 1.9 | 1.9 | 3.901437372%
WSL20106L000FEA18 | Resistor | R1 | 2010 | Res1_2 | 1 | 0.006 | 1.72 | 1.72 | 3.531827515%
Res1 | Resistor | R3, R4, R5, R7, R11 | R0805 | Res1 | 1 | 100k | 0.17 | 0.17 | 0.3490759754%
Res1 | Resistor | R9 | R0805 | Res1_4 | 1 | 5k1 | 0.17 | 0.17 | 0.3490759754%
Cap | Capacitor | C11, C12, C13 | C0805 | Cap_1 | 1 | 2n7 | 0.28 | 0.28 | 0.5749486653%
Cap | Capacitor | C1, C4, C5, C6, C9, C10, C14, C15, C18, C21, C22 | C0805 | Cap | 1 | 100n | 0.28 | 0.28 | 0.5749486653%
 |  |  |  |  |  |  |  | 4.52 | 9.281314168%
Debug
4-1437565-1 | Switch | S1 | SMD | SW-PB | 1 |  | 0.06 | 0.06 | 0.1232032854%
Res1 | Resistor | R2, R12, R13 | R0805 | Res1_6 | 1 | 1k | 0.17 | 0.17 | 0.3490759754%
Plug | Test point | P1, P4, P5, P7, P9, P10 | HDR1X1 | Test point | 6 |  | 0.05 | 0.3 | 0.6160164271%
KPTL-3216SURCK-01 | KINGBRIGHT RED LED | D8 | SMD | LED2 | 1 |  | 1.83 | 1.83 | 3.757700205%
 |  |  |  |  |  |  |  | 2.36 | 4.845995893%
 |  |  |  |  |  |  | Total | 48.7 | 100%

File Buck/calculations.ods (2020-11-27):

Dénomination | Valeur | Unité | Commentaire | Valeur définie par cahier des charges / datasheet
 |  |  |  | Valeur théorique calculée
 |  |  |  | Valeur pratique choisie
Données
Vin min | 24 | V | Sortie du panneau solaire, entrée du buck
Vin max | 50 | V
Vin nom | 36 | V
Pout nom | 200 | W | Sortie du buck
Vout min | 22 | V
Vout max | 28 | V
Iout max | 9 | A
Rendement | 92% |  | @150W
ResADC | 12 | bits | cf datasheet STM32L476RG
Fsw | 150 | kHz | Fréquence de découpage du MOS
Mesure tension
Vin max | 55 | V | Facteur de sécurité sur tension max : +20%
I meas | 500 | uA | Courant dans pont diviseur
Vadc max | 3,3 | V | Vref ADC
Divider ratio | 17 |  | Ratio Vin/Vadc
Rtot | 110 | kΩ | Rtot=R1+R2, R1 entre masse et ADC, R2 entre ADC et Vin
R2 | 103,4 | kΩ | R2=Rtot-R1
R1 | 6,6 | kΩ | R1=Rtot/Ratio
R2 | 100 | kΩ | Valeurs choisies selon valeurs idéales précédentes
R1 | 6,2 | kΩ
Vin max | 56,5 | V | Vin max avec valeurs choisies précédemment
Pdiss | 30 | mW | Puissance dissipée par la mesure
NbcountsADC | 4096
Resolution | 14 | mV | ADC LSB step size
Mesure courant
I max | 10 | A | Courant max mesurable
Rshunt | 6 | mΩ | Coisi pour un bon ratio entre Vshunt et Pshunt | WSL20106L000FEA18
Vshunt | 60 | mV | Tension max shunt
Pshunt | 600 | mW | Pmax shunt
Amp gain max | 55 |  | Unidirectional gain ! Divide by two if bidir
Amp gain | 51 |  | Chosen gain, match to selected amplifier ic. Should be less than previously calculated gain
R1 | 100 | Ω | Résistance gain LTC6101, high side (set for 1mA output current)
R2 | 5,1 | kΩ | Résistance gain LTC6101, low side
Vmeas max | 3,06 | V | ADC voltage at full current, should be less than V ADC max
Resolution | 2,6 | mA | ADC LSB step size
L
ΔI | 700 | mA | Ondulation du courant dans l'inductance max
VinL | 36 | V
VoutL | 12 | V
Ton | 2,222222222 | µs
Toff | 4,444444444 | µs
DutyCycle | 33%
Lmin | 76,19047619 | µH
Lmax | 200 | µH
Lchosen | 120 | µH |  | 1140-121K-RC
DCR | 28 | mΩ
ΔI | 444,4444444 | mA | Ondulation du courant réelle
Cin
C | 100 | uF |  | EEVFK1K101Q
Irms | 50 | mA
ESR | 320 | mΩ
Cout
ΔV | 0,5 | V | Desired ripple voltage at the output
C | 3,0 | µF
C | 9,4 | µF | Prendre en compte le courant RMS | 100ZLJ220M12.5X25
ESR C choisi | 450 | mΩ |  | C'est le plus petit condo en stock avec le bon Irms
Δvout réel | 0,357604413 | V | ΔI*ESRC+(ΔI*(1/Fsw)*0,5)/C
 |  |  |  |  | cgs
MOS |  |  |  |  | vt | 2 | V
 |  |  |  |  | vgs0 | 4,5 | V
Rdson | 11 | mΩ |  | SIR120DP-T1-RE3 | imgd | 2,27 | A | défini par R
Qc | 120 | nC | Gate charge |  | Img | 2 | A | I max du driver
Dmax | 67% |  | Max duty cycle (Vin=36V, vout=24V)
I(av) | 6,0 | A
Pstat | 0,396 | W | Rdson*(Duty(mos)*Iout)²
Pdyn |  | W
RθJA | 62 | °C/W | Junction to ambient
RθJC | 0,9 | °C/W | Junction to sink, greased
Tj | 50 | °C | Junction, static power & no heatsink
Diode
Dmin | 25% |  | Min duty cycle (Vin=48V, Vout=12V) | STPS30L60C
If(av) | 6,75 | A | Average forward current
Vf | 420 | mV | Forward voltage @ Imax
Pstat | 2,84 | W | P = Vf x IF(AV)+ 0.02 x IF²(RMS)
RθJA | 40 | °C/W | Junction to ambient, for 2,5cm² 35µ copper area, D²PAK | (35°C/W for 7,5cm² copper)
Tj | 139 | °C | Junction, static power & no heatsink
Cj | 0,6 | nF | Junction capacitance @ 30V reverse
Pertes statiques
Diode | 2,84 | W
MOS | 0,40 | W
Current sense | 0,60 | W
Voltage sense | 0,06 | W | 2 Etages de mesure
L | 2,27 | W | DCR*Iout²
C | 0,09 | W | ESR*ΔI²
Conso µC | 1,00 | W | Regulateur linéaire : I@5V = I@12V !
Total static | 7,25 | W
Static Eff | 96,5% |  | Rendement estimé sur pertes statiques uniquement, @200W
Pertes dynamiques
Diode | 0 | W
MOS | 0 | W
Conso driver | 0 | W | ?
Total dyn | 0 | W | Pertes dynamiques uniquement
Total loss | 7,25 | W | Pertes statiques + dynamiques
Total eff | 96,5% |  | Rendement total estimé @200W

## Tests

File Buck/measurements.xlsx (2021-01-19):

Vout | 4096 | cnt | 56.52580645 | V
Iout | 379 | cnt | 1.017822266 | A
Iout | 10 | A | 3.06 | V
 |  |  | 3798.109091 | cnt
 |  |  | 55100
Vin=45V, CV 24V
V | Iout | Iin(45V,A) | Iin(12V,mA) | Pout | Pin(45V) | Pin(12V) | Pin tot | Vin=45V, Vout=24V | Loss
23.5 | 1.386 | 0.78 | 72 | 32.571 | 35.1 | 0.864 | 35.964 | 90.56556557% | 2.529
23.65 | 1.689 | 0.95 | 72 | 39.94485 | 42.75 | 0.864 | 43.614 | 91.5872197% | 2.80515
23.75 | 2.065 | 1.15 | 72 | 49.04375 | 51.75 | 0.864 | 52.614 | 93.21425856% | 2.70625
23.86 | 2.46 | 1.36 | 72 | 58.6956 | 61.2 | 0.864 | 62.064 | 94.57269915% | 2.5044
23.92 | 2.957 | 1.63 | 72 | 70.73144 | 73.35 | 0.864 | 74.214 | 95.30740831% | 2.61856
24 | 3.562 | 1.97 | 72 | 85.488 | 88.65 | 0.864 | 89.514 | 95.50237952% | 3.162
24 | 4.03 | 2.22 | 72 | 96.72 | 99.9 | 0.864 | 100.764 | 95.9866619% | 3.18
24 | 4.57 | 2.51 | 72 | 109.68 | 112.95 | 0.864 | 113.814 | 96.36775792% | 3.27
23.9 | 5.02 | 2.74 | 72 | 119.978 | 123.3 | 0.864 | 124.164 | 96.62865243% | 3.322
23.9 | 5.41 | 2.95 | 72 | 129.299 | 132.75 | 0.864 | 133.614 | 96.770548% | 3.451
23.78 | 5.98 | 3.25 | 72 | 142.2044 | 146.25 | 0.864 | 147.114 | 96.66272415% | 4.0456
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

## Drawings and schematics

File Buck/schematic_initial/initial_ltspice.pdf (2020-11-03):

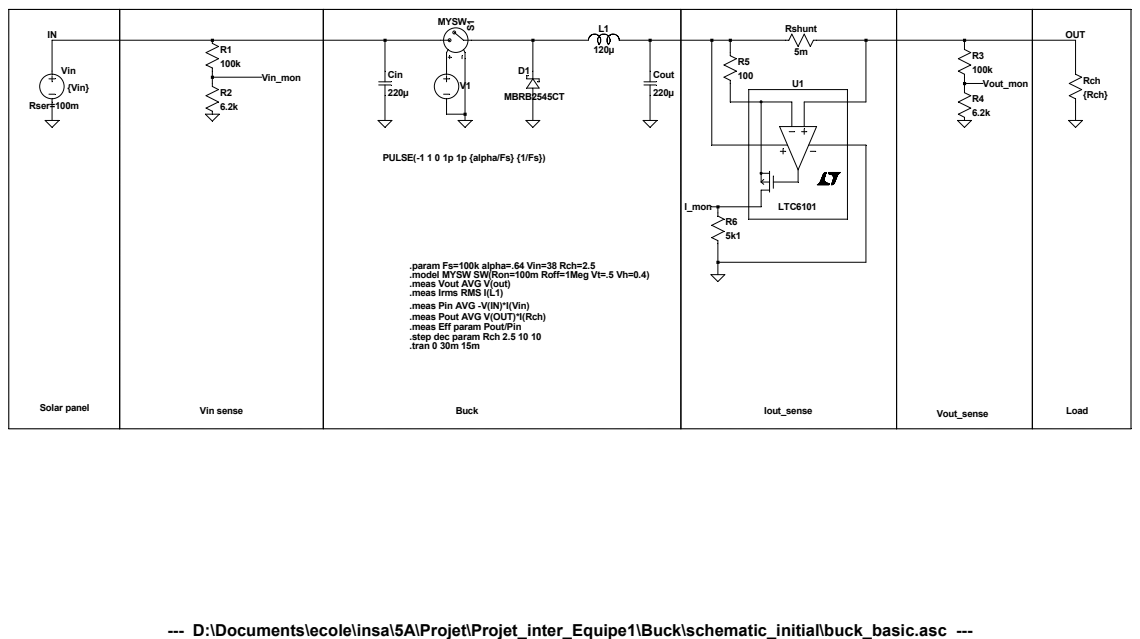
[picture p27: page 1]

PULSE(-1 1 0 1p 1p {alpha/Fs} {1/Fs})

.param Fs=100k alpha=.64 Vin=38 Rch=2.5
.model MYSW SW(Ron=100m Roff=1Meg Vt=.5 Vh=0.4)
.meas Vout AVG V(out)
.meas Irms RMS I(L1)
.meas Pin AVG -V(IN)*I(Vin)
.meas Pout AVG V(OUT)*I(Rch)
.meas Eff param Pout/Pin
.step dec param Rch 2.5 10 10
.tran 0 30m 15m

--- D:\Documents\ecole\insa\5A\Projet\Projet_inter_Equipe1\Buck\schematic_initial\buck_basic.asc ---

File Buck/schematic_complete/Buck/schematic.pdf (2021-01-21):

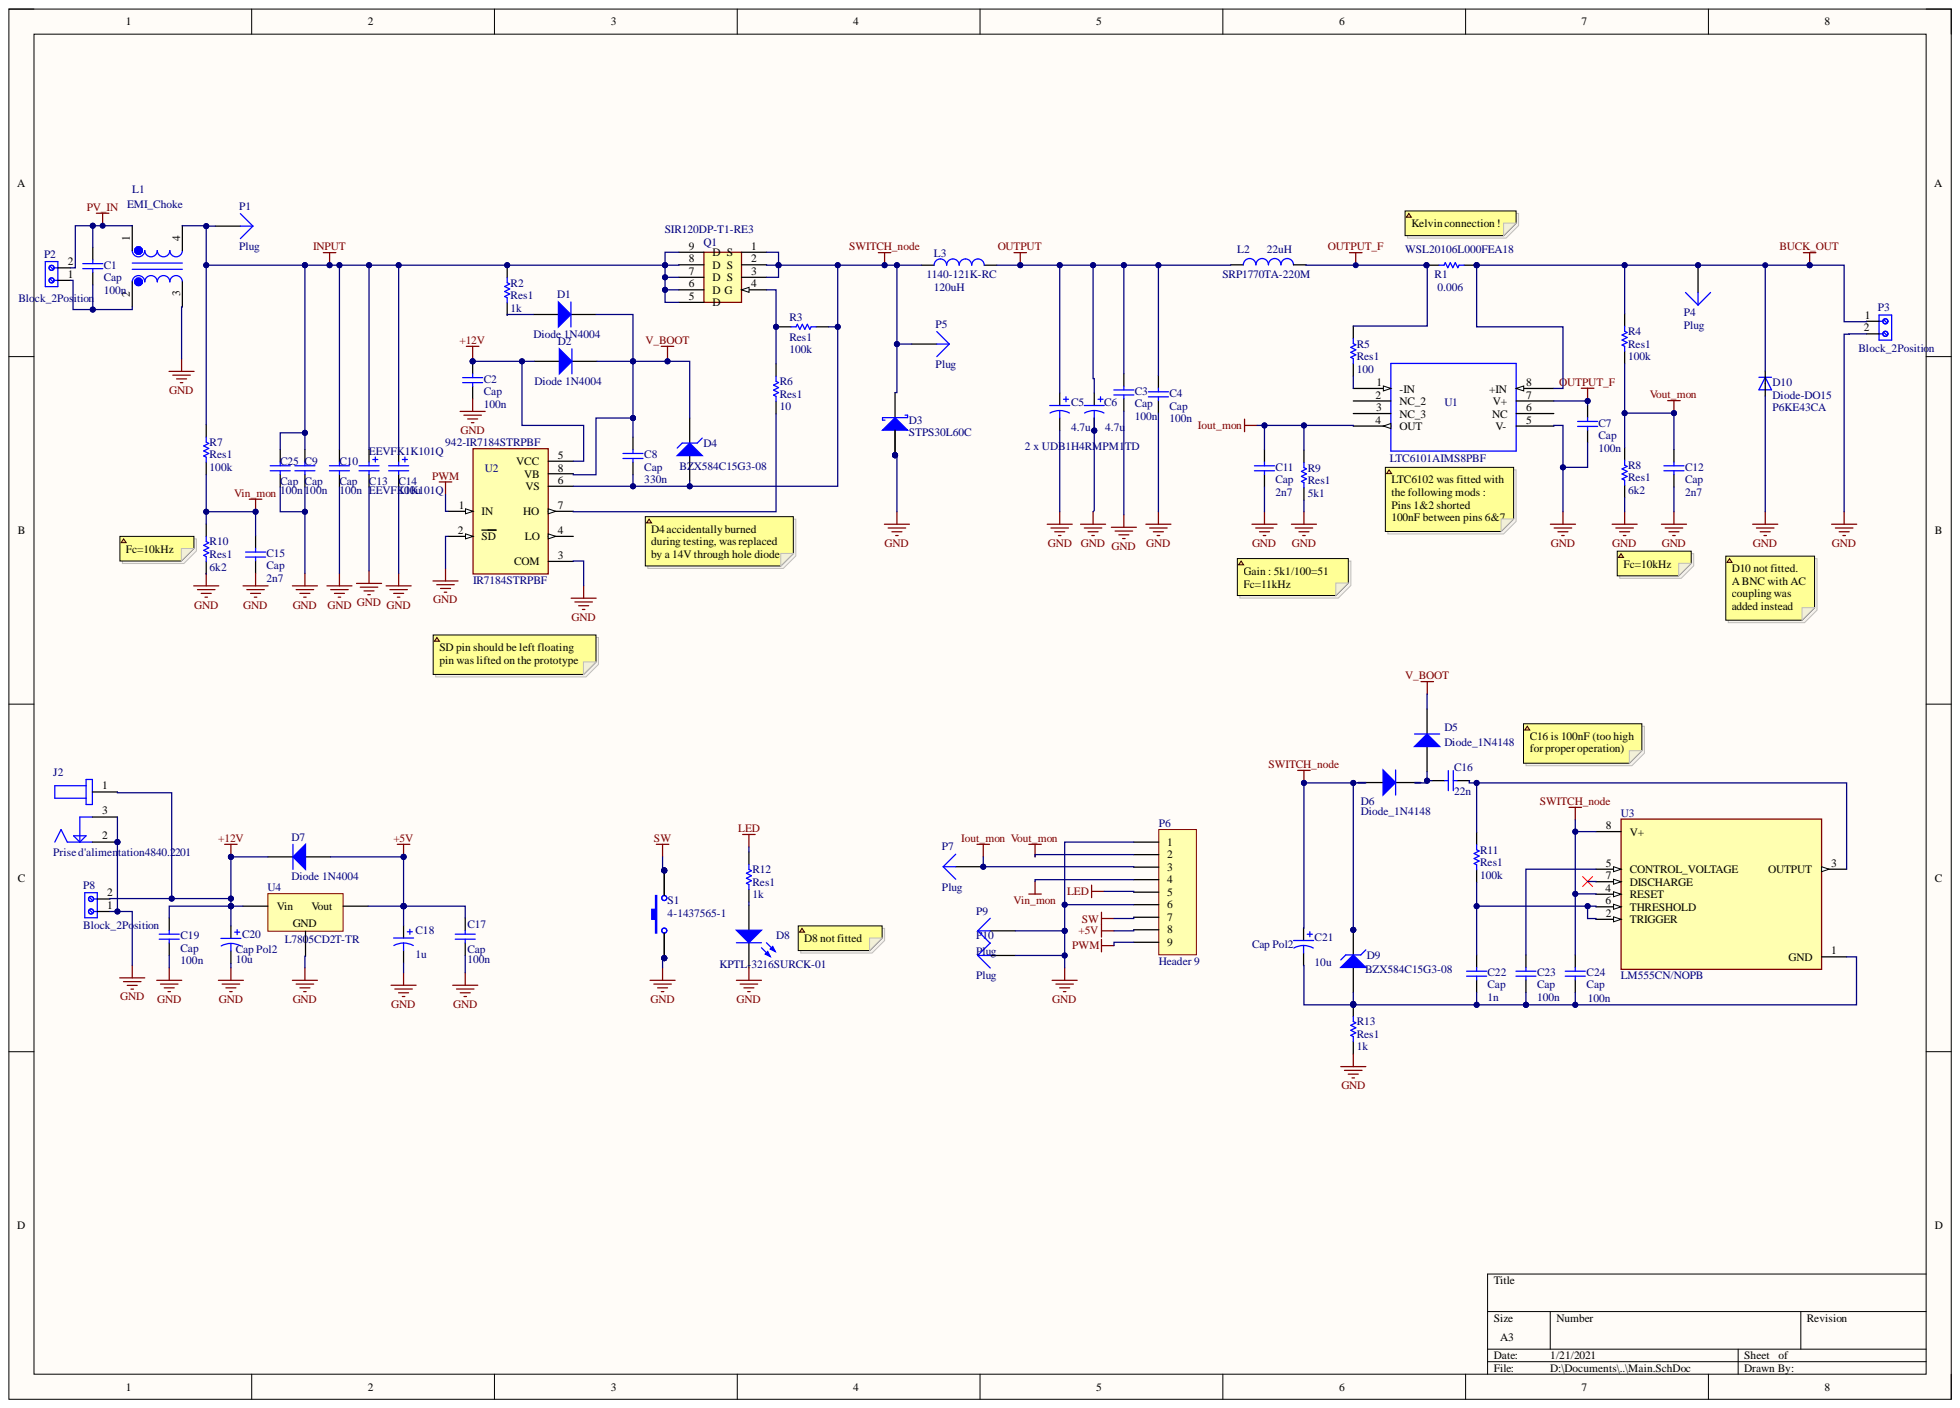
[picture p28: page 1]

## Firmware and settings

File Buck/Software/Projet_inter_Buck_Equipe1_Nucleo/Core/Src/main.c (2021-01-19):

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
/* Includes ------------------------------------------------------------------*/
#include "main.h"

/* USER CODE BEGIN Includes */
#include <stdio.h>
#include "Buck.h"


/* USER CODE END Includes */

ADC_HandleTypeDef hadc1;
DMA_HandleTypeDef hdma_adc1;

TIM_HandleTypeDef htim1;
TIM_HandleTypeDef htim2;

UART_HandleTypeDef huart2;

void SystemClock_Config(void);
static void MX_GPIO_Init(void);
static void MX_DMA_Init(void);
static void MX_USART2_UART_Init(void);
static void MX_ADC1_Init(void);
static void MX_TIM1_Init(void);
static void MX_TIM2_Init(void);
/**
  * @brief  The application entry point.
  * @retval int
  */
int main(void)
{
  /* MCU Configuration--------------------------------------------------------*/

  /* Reset of all peripherals, Initializes the Flash interface and the Systick. */
  HAL_Init();

  /* Configure the system clock */
  SystemClock_Config();

  /* Initialize all configured peripherals */
  MX_GPIO_Init();
  MX_DMA_Init();
  MX_USART2_UART_Init();
  MX_ADC1_Init();
  MX_TIM1_Init();
  MX_TIM2_Init();
  /* USER CODE BEGIN 2 */

  Set_Duty_OL(0);
  Reg_Mode=REG_MODE_CV;
  SetVout(24.0);
  SetI(1.0);
  HAL_ADC_Start_DMA(&hadc1,(uint32_t *)&ADC_buffer, 3);
  HAL_TIM_Base_Start_IT(&htim2);
  HAL_ADC_Start_IT(&hadc1);

  HAL_TIM_PWM_Start(&htim1, TIM_CHANNEL_1);


  /* USER CODE END 2 */

  /* Infinite loop */
  /* USER CODE BEGIN WHILE */
  float v=24.0, increment=1.0;
  unsigned char c=' ';
	printf("Buck started\r\n");
  while (1)
  {
    /* USER CODE END WHILE */

    /* USER CODE BEGIN 3 */
		//HAL_GPIO_TogglePin(LD2_GPIO_Port, LD2_Pin);
	  HAL_UART_Receive(&huart2, &c, 1, 10);
	  switch(c){
	  case 'v':
		  printf("Switched to CV mode\r\n");
		  Reg_Mode=REG_MODE_CV;
			SetVout(24.0);
			v=24.0;
			increment=1.0;
		  break;
	  case 'c':
		  printf("Switched to CC mode\r\n");
		  Reg_Mode=REG_MODE_CC;
			SetI(0.5);
			v=0.5;
			increment=0.25;
		  break;
	  case 'o':
		  printf("Switched to OL mode\r\n");
		  Reg_Mode=REG_MODE_OL;
			Set_Duty_OL(0.1);
			v=0.1;
			increment=0.05;
		  break;
	  case 'm':
		  printf("Switched to MPPT mode\r\n");
		  Reg_Mode=REG_MODE_MPPT;
		  Iout_set=400;
		  I_inc=1;
		  cnt=0;
		  break;
	  case '+':
		  v+=2*increment;
	  case '-':
		  v-=increment;
		  printf("SetPoint : %.2f\r\n",v);
			switch(Reg_Mode){
			case REG_MODE_CV :
				SetVout(v);
				break;
			case REG_MODE_OL:
				Set_Duty_OL(v);
				break;
			case REG_MODE_CC :
				SetI(v);
				break;
			}
		  break;
	  default:
		  break;
	  }
	  c=' ';
		if(!HAL_GPIO_ReadPin(B1_GPIO_Port,B1_Pin)){
			printf("B1 pressed !\r\n");

		}else if(!HAL_GPIO_ReadPin(B2_GPIO_Port,B2_Pin)){
			printf("B1 pressed !\r\n");
		}
		HAL_Delay(500);
		printBuckStatus();
  }
  /* USER CODE END 3 */
}

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
/* USER CODE BEGIN 4 */
int __io_putchar(int ch){
	uint8_t c[1];
	c[0] = ch & 0x00FF;
	HAL_UART_Transmit(&huart2, &*c, 1, 10);
	//HAL_Delay(1);
	return ch;
}

int _write(int file,char *ptr, int len){
	int DataIdx;
	for(DataIdx= 0; DataIdx< len; DataIdx++){
		__io_putchar(*ptr++);
	}
	return len;
}


void HAL_TIM_PeriodElapsedCallback(TIM_HandleTypeDef *htim){
}

void HAL_ADC_ConvCpltCallback(ADC_HandleTypeDef* hadc){
	HAL_GPIO_WritePin(LD2_GPIO_Port, LD2_Pin,1);
	Vout_mon = .99*Vout_mon + .01*ADC_buffer[0];
	Vin_mon = .99*Vin_mon + .01*ADC_buffer[1];
	I_mon = .99*I_mon + .01*ADC_buffer[2];

	switch(Reg_Mode){
	case REG_MODE_CV :
		RegulateCV();
		break;
	case REG_MODE_OL:
		Set_Duty_Cycle();
		break;
	case REG_MODE_CC :
		RegulateCC();
		break;
	case REG_MODE_MPPT:
		RegulateMPPT();
		//Set_Duty_OL(0.1);
		break;
	default :
		break;
	}
	HAL_GPIO_WritePin(LD2_GPIO_Port, LD2_Pin,0);

}

/* USER CODE END 4 */
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


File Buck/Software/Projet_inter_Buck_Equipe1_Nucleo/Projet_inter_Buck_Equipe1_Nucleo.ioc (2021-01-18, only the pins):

Mcu.UserName=STM32L476RGTx
PA2.Signal=USART2_TX
PA3.GPIO_Label=USART_RX
PA3.Signal=USART2_RX
PA5.GPIO_Label=LD2 [green Led]
PA5.Signal=GPIO_Output
PA8.Signal=S_TIM1_CH1
PB13.GPIO_Label=LD1
PB13.Signal=GPIO_Output
PC0.Signal=ADCx_IN1
PC1.Signal=ADCx_IN2
PC13.GPIO_Label=B1 [Blue PushButton]
PC13.Signal=GPXTI13
PC2.Signal=ADCx_IN3
PC4.GPIO_Label=B2
PC4.Signal=GPIO_Input

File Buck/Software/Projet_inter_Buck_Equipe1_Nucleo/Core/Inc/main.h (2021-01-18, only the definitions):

#define B1_Pin GPIO_PIN_13
#define B1_GPIO_Port GPIOC
#define USART_RX_Pin GPIO_PIN_3
#define USART_RX_GPIO_Port GPIOA
#define LD2_Pin GPIO_PIN_5
#define LD2_GPIO_Port GPIOA
#define B2_Pin GPIO_PIN_4
#define B2_GPIO_Port GPIOC
#define LD1_Pin GPIO_PIN_13
#define LD1_GPIO_Port GPIOB
#define TMS_Pin GPIO_PIN_13
#define TMS_GPIO_Port GPIOA
#define TCK_Pin GPIO_PIN_14
#define TCK_GPIO_Port GPIOA
#define SWO_Pin GPIO_PIN_3
#define SWO_GPIO_Port GPIOB

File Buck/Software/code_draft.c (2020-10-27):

#include <stdio.h>
#define FCY 16000000UL
#include <libpic30.h>
#include "mcc_generated_files/mcc.h"
#include "mcc_generated_files/system.h"


//ADC scaling coefficients
#define KVOUTMON (6.2/(110.0+6.2))  //Vout_mon divider
#define KVINMON (6.8/(100.0+6.8))  //Vin_mon divider
#define KIMON (.005*50.0)          //I_mon Rshunt * CSAmp gain
#define VCC (3.3)

#define REGMODE_CV      0   //Constant voltage mode, call setVout())
#define REGMODE_CC      1   //Constant current mode, call setI())
#define REGMODE_MPPT    2   //MPPT mode
#define REGMODE_OL      3   //Open Loop mode, call setDuty())

uint8_t regMode = REGMODE_OL;           //Regulation mode
uint16_t vout_mon, vin_mon, i_mon, pot; //ADC values (0-4095)
uint16_t duty_cycle=100;
bool state=0;                           //temporary
uint16_t vout_set, i_set;               //Target values (0-4095))

void setVout(float target){
    vout_set=(target)*(KVOUTMON)*4096.0/(VCC);
}
void setI(float target){
    i_set=(target)*(KIMON)*4096.0/(VCC);
}
void setDuty(float target){
    duty_cycle=(target)*TMR1_Period16BitGet();
}
void setRegMode(uint8_t mode, float target){
    regMode=mode;
    switch(regMode){
         case REGMODE_CV :
            setVout(target);
            break;
        case REGMODE_CC :
            setI(target);
            break;
        case REGMODE_MPPT :
            //TODO 
            break;
        case REGMODE_OL :
            setDuty(target);
            break;
    }
}

float getVin(void){
    return vin_mon/4096.0*VCC/KVINMON;
}
float getI(void){
    return i_mon/4096.0*VCC/KIMON;
}
float getVout(void){
    return vout_mon/4096.0*VCC/KVOUTMON;
}
float getDuty(void){
    return (float)duty_cycle/TMR1_Period16BitGet();
}

void TIM2_ISR(void){
    
    
	vout_mon = ADC1_GetConversion(Vout_mon);
	i_mon = ADC1_GetConversion(I_mon);
	pot = ADC1_GetConversion(Pot);
	
	
    switch(regMode){
        case REGMODE_CV :
            if(vout_mon<vout_set){
                duty_cycle++;
            }else if(vout_mon>vout_set){
                duty_cycle--;
            }
            break;
        case REGMODE_CC :
            if(i_mon<i_set){
                duty_cycle++;
            }else if(i_mon>i_set){
                duty_cycle--;
            }
            break;
        case REGMODE_MPPT :
            //TODO 
            break;
        case REGMODE_OL :   //Direct pot reading
            duty_cycle=1+(((TMR1_Period16BitGet()-1)*(uint32_t)pot)/4096);
            break;
    }
    
    //saturate duty cycle
    if(duty_cycle>(TMR1_Period16BitGet()-1))duty_cycle=TMR1_Period16BitGet()-1;
    else if(duty_cycle<1)duty_cycle=1;
    
    //assign duty cycle to output
    OC1_SecondaryValueSet(duty_cycle);
}
int main(void){
    SYSTEM_Initialize();
    TMR2_SetInterruptHandler(TIM2_ISR);
    
    //TMR1 : 125n - 4.096m , 8MHz - 244Hz : 20u = 50kHz = 0x13F //13u = 75kHz
    //TMR2 : 125n - 4.096m , 8MHz - 244Hz : 500u = 2kHz = 0x1F3F
    TMR2_Start();   //ADC timer, 2kHz
    TMR1_Start();   //PWM timer, 50kHz
    OC1_Start();    //Output compare : PWM
    
    printf("Hello world !\r\n");
    setI(10.0);
    setVout(5.0);
    
    LED0_Toggle();
    
    while (1){
        __delay_ms(10);
        printf("Vin : %.2f\tVout : %.2f\tPot : %d\tduty : %.2f\r\n",(double)getVin(),(double)getVout(),pot,(double)getDuty());
        __delay_ms(1000);
        
        if(BUTTON_GetValue() != state){	//Toggle button between CV & OL
            state=!state;
            if(state){
                LED0_Toggle();
                if(regMode == REGMODE_CV){
                    regMode = REGMODE_OL;
                    printf("Switched to OL mode\r\n");
                }else{
                    regMode = REGMODE_CV;
                    printf("Switched to CV mode\r\n");
                }
            }
            __delay_ms(1000);	//Crude button debounce
        }
    }
    return 1;
}

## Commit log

2020-04-30 added second sheet to calculations
    [calculations.ods]
2020-09-21 modified buck Readme.md
2020-09-26 added calculations
    [calculations.ods]
2020-09-30 added buck calculations
    [calculations.ods]
2020-10-07 added basic buck schematic
2020-10-15 updated calculations
    [calculations.ods]
2020-10-16 modified vsense resistors
2020-10-27 added PIC sample code for early prototype
2020-10-30 added excel update
    [calculations.ods]
2020-10-31 Added altium project
    [Buck.PrjPcb]
2020-11-01 created schematic pdf
    [Buck.PrjPcb, Main.SchDoc, Sheet1.SchDoc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]
2020-11-03 added parts from stock
    [calculations.ods]
2020-11-03 updates capacitor values
2020-11-03 updated altium schematic to match selected components
    [Buck.PrjPcb, Main.SchDoc, calculations.ods]
2020-11-04 Ajout de la schématique BMS
    [BMS_Footprints.PcbLib, BMS_GEI_Corp.PrjPcb, BMS_Gauges_and_measure.SchDoc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]
2020-11-05 pcb refactor
    [main.PcbDoc]
2020-11-05 Mise a jour projet altium
    [BMS_Switch_and_batteries.SchDoc]
2020-11-06 updates calculations and schematic
    [Main.SchDoc, calculations.ods]
2020-11-07 Mise à jour de la schématique avec level shifter et ports JTAG
    [BMS_Footprints.PcbLib, BMS_Gauges_and_measure.SchDoc, BMS_Main.SchDoc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]
2020-11-10 modified schematic per prof request
2020-11-10 updated buck schematic
    [Main.SchDoc]
2020-11-10 update schematic
    [BMS_GEI_Corp.PrjPcb, BMS_Gauges_and_measure.SchDoc, BMS_Main.SchDoc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]
2020-11-10 update bms schematic
    [BMS_GEI_Corp.PrjPcb, BMS_Gauges_and_measure.SchDoc, BMS_Main.SchDoc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]
2020-11-10 Ajout des connecteurs Buck input et load output + ajout capa decouplage + ajout des footprints que j'ai pu trouver
    [BMS_Footprints.PcbLib, BMS_GEI_Corp.PrjPcb, BMS_Main.SchDoc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]
2020-11-17 Premier programme SW BMS
2020-11-17 Ajout des différents footprints, Schématique corrigée avec indications de Rocacher, manque juste footprint du bornier à vis
    [BMS_AMain.SchDoc, BMS_Footprints.PcbLib, BMS_GEI_Corp.PrjPcb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]
2020-11-18 added bom per function
    [Bom_per_function_preliminary.xlsx]
2020-11-19 updated schematic
    [Main.SchDoc]
2020-11-20 buck schematic wrapup
    [Buck.PcbLib, Buck.PrjPcb, Buck.SCHLIB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]
2020-11-20 added BOM
    [BOM.xlsx]
2020-11-20 Ajout des points de test et du cartouche
    [BMS_AMain.SchDoc, BMS_GEI_Corp.PrjPcb, BMS_Gauges_and_measure.SchDoc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]
2020-11-20 updated per TR request : added diode, changed c14
    [Main.SchDoc]
2020-11-22 Corrections rocacher sauf 5V et nucleo shield
    [BMS_Footprints.PcbLib, BMS_Schematic.SchLib, BMS_Switch_and_batteries.SchDoc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]
2020-11-22 correc R4R5
    [BMS_Switch_and_batteries.SchDoc]
2020-11-22 remplacement shield par simple connecteurs
    [BMS_AMain.SchDoc, BMS_Footprints.PcbLib, BMS_GEI_Corp.PrjPcb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]
2020-11-22 updated schematic per A.B. request
    [Buck.PrjPcb, Buck.SCHLIB, Main.SchDoc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]
2020-11-25 -maltium started component placement
    [Buck.PrjPcb, Buck.SCHLIB, Main.SchDoc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]
2020-11-26 preliminary buck component placement
    [Main.SchDoc, main.PcbDoc]
2020-11-27 buck layout start
    [BOM.xlsx, Buck.PcbLib, Buck.PrjPcb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]
2020-11-27 Modification commande double NMOS
    [BMS_Footprints.PcbLib, BMS_GEI_Corp.PrjPcb, BMS_Schematic.SchLib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]
2020-11-27 tous footprints OK
    [BMS_Footprints.PcbLib, BMS_GEI_Corp.PrjPcb]
2020-12-02 debut routage : debut placement composants avec pleins d'erreurs
    [BMS.PcbDoc, BMS_AMain.SchDoc, BMS_GEI_Corp.PrjPcb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]
2020-12-03 -madded second pcb version
    [Buck.PrjPcb, Buck.SCHLIB, Main.SchDoc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]
2020-12-03 added schematic pdf
2020-12-04 nveau pcbdoc
    [BMS.PcbDoc, BMS2.PcbDoc, BMS_GEI_Corp.PrjPcb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]
2020-12-04 placement puissance
    [BMS2.PcbDoc, BMS_Footprints.PcbLib, BMS_GEI_Corp.PrjPcb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]
2020-12-06 Routage V1
    [BMS2.PcbDoc, BMS_Footprints.PcbLib, BMS_Gauges_and_measure.SchDoc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]
2020-12-07 Première version routage hell yeah
    [BMS2.PcbDoc]
2020-12-08 Modifs alex
    [BMS2.PcbDoc, BMS_Footprints.PcbLib, BMS_GEI_Corp.PrjPcb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]
2020-12-11 Routage final
    [BMS2.PcbDoc, BMS_GEI_Corp.PrjPcb]
2020-12-13 final routing
    [main_v2.PcbDoc]
2020-12-14 changes per A.B. request
    [Buck.PcbLib, Buck.SCHLIB, Main.SchDoc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]
2020-12-14 BOM cleanup
    [BOM.xlsx, BOM3.xlsx]
2020-12-14 Modifications taille trous + ajout trous fixation mecaniques
    [BMS2.PcbDoc, BMS_Footprints.PcbLib, BMS_Gauges_and_measure.SchDoc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]
2021-01-18 added measurements excel
    [measurements.xlsx]
2021-01-18 added measurements
    [measurements.xlsx]
2021-01-19 correction du routage
    [BMS2.PcbDoc, BMS_GEI_Corp.PrjPcb]
2021-01-19 code update
    [measurements.xlsx]
2021-01-19 pcb view
2021-01-20 Ajout du fichier InfoBatt.c implémentant trois fonctions principales ainsi que deux fonctions en support
2021-01-20 Ajout des fonctions pour la gestion des jauges (InfoBatt.c .h) ainsi que la gestion de la communication par I2C (i2c.c .h)
2021-01-20 Correction des erreurs d'intégration et d'include
    [BMS_Management.c, InfoBatt.c, i2c.c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]
2021-01-20 Ajout de la méthode BMSManagement_getLastStatus sur le fichier BMSManagement.c + correction de bugs
    [BMS_Management.c]
2021-01-20 Relecture et ajout de commentaires - Document terminé
2021-01-20 v1.0 - Version finale sans gestion des erreurs par UART

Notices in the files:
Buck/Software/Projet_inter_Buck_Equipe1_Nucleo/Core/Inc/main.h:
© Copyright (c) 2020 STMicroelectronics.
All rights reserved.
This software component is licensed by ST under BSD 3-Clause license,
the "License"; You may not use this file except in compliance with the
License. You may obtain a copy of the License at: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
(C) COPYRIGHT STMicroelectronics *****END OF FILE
